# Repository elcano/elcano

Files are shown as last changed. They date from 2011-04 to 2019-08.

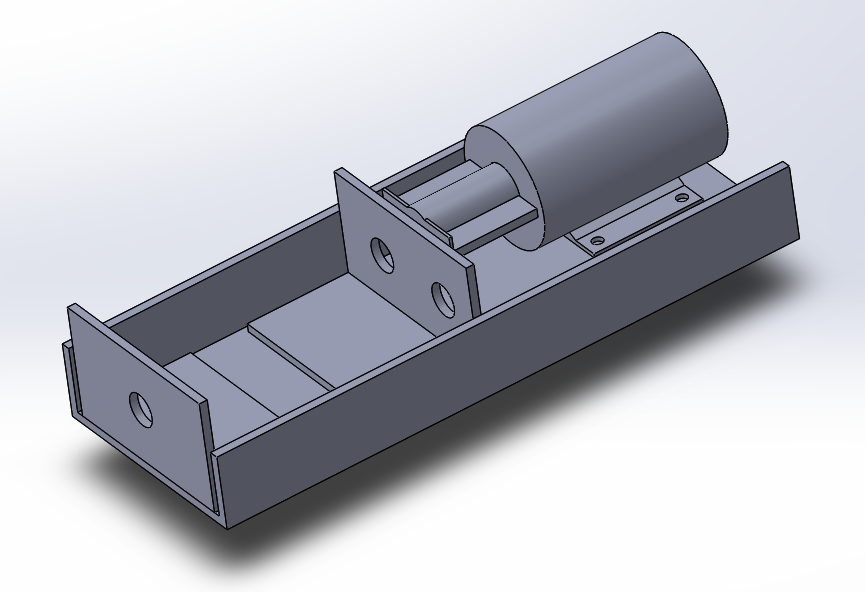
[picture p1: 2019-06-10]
Mechanical/ELF/Brake_System/Brake_System.PNG

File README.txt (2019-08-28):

Welcome to the Elcano autonomous tricycle project!
Please see:
http://www.elcanoproject.org/

This repository has been archived. The system consists of several different microprocessors. Elcano/Elcano has been broken into separate repositories for each processor.

To get started, fork and clone the repository:
https://github.com/elcano/elcano

Parameters and settings for each trike are defined in:
/libraries/Settings/Settings.h

Place the contents of the libraries folder into your libraries folder under
Arduino/libraries

The repository includes examples in the file:
Arduino/libraries/Settings/SettingsTemplate.h

Only libraries/Settings/SettingsTemplate.h should be committed in the
repository -- the Arduino/libraries/Settings/Settings.h file is site-specific.

-- Copy
   Arduino/libraries/Settings/SettingsTemplate.h
   to
   Arduino/libraries/Settings/Settings.h
-- Give your trike a different VEHICLE_NUMBER value.
-- Add your own trike's settings, following the examples.
-- Put your settings in a conditional for your new VEHICLE_NUMBER value.

When you pull in updates from the main repository, look for changes in
SettingsTemplate.h and if needed merge them with your own Settings.h.
Especially watch for new trike parameters used in sketches.

Sketches that need these settings should
#include <Settings.h>
*after* all other includes or definitions that are used in Settings.h.

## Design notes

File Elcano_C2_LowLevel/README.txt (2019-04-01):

In Settings.h
DEBUG enables serial printing of debug messages
RELAYInversion 
LLBversion defines which settings file should be used for the low level board

TESTING disables including hardware specific libraries like Arduino.h
testing is defined in the source code for unit testing

The libraries you will need are:
CAN_BUS_Shield by Seeed-Studio	
	https://github.com/Seeed-Studio/CAN_BUS_Shield

PID by Brett Beauregard
	https://github.com/br3ttb/Arduino-PID-Library

Pin Change Interrupt by Nico Hood
	https://github.com/NicoHood/PinChangeInterrupt

Builit-in 
SPI library
Servo library

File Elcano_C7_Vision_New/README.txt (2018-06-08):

Elcano Line Detection:

Updated 4/2/2018
Author: Conor Van Achte

How to use:
1. Make sure the Raspi Camera is detected by the OS by running this 
   command in console "vcgencmd get_camera".
2. If the camera is connected, you may need to enable the camera for use.
   This can be done by entering the command "sudo modprobe bcm2835-v4l2".
   This command opens up the camera for use by the OS.
3. Compile the program by running entering "g++ -std=c++11 $(pkg-config --libs --cflags opencv) -o LineTest LineDetectionMain.cpp" in console.
   (Optional) To run the program with communication to arduino add rs232.c to the compilation string.
4. Run the program with ./LineTest.
5. Exit the program by pressing the ESC key.

How does it work?

The Elcano Line Detection works by use of the Raspi Camera on the Raspi. As of 4/2/2018, the Line Detection code detects yellow lines, and 
has a filter for yellow colors. The program takes a frame as input from the camera, uses a yellow filter mask
on the image to isolate the yellow colors, and then applies a Gaussian blur to smooth out the image.
A Canny edge detector is then applied to the frame to detect the edges found in the image.
Finally a HoughLine transform is performed to draw detect lines on the image. The Elcano Line Detection program will then find the average
of the lines found, and draw an averaged line on the frame every 5 frames.This code is currently in testing
and will need refactoring and possible a new implementation for full lane detection.

Update 05/03/2018

Elcano Line Detection code has been refactored and appears to be working reasonably well with the arduino sketch Kyle Farmer wrote. The Line Detection
program is running much smoother after a reduction in GaussianBlur from a 25x25 matrix down to a 9x9 and finally to a 3x3. The Pi sends information to the
arduino mega, which then provides instructions to the servomotor on which direction to turn. Currently we have a Raspi connected to
an arduino mega via serial connection, and the arduino mega is connected to a small servo motor that rotates based on the values found by the raspi.

Additional Information:

The Elcano Line Detection code was written using Visual Studio. In order to compile you may need to install the additional libraries provided by
OpenCV. A link to setup Visual Studio with OpenCV can be found here: https://www.youtube.com/watch?v=l4372qtZ4dc.

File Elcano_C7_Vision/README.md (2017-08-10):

Elcano Vision Subsystem
=======================

This is the subcomponent of the Elcano project that uses a Raspberry Pi
to scan the area for obstacles with OpenCV.

Dependencies
------------

- [opencv (v3.2)](http://opencv.org) (object detection)
- [raspicam](https://github.com/cedricve/raspicam) (raspberry pi camera interface)

Build Instructions
------------------

1. Compile rs232:
	gcc -c rs232.c -o rs232.o

2. Compile main:
	g++ -std=c++11 $(pkg-config --libs --cflags opencv) -o main main.cpp rs232.o

Developer Overview
------------------

- `main.cpp`: The driver function
- `rs232.c`: Allows serial communication between Raspberry Pi and Arduino

Todo
----

- Improve reliability/accuracy of cone location with Kalman Filter
- Add makefile for building
- Add comments to main

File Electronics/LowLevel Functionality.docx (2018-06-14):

This document:

License:

Functionality:

The LowLevel is a printed circuit board (PCB) designed for land vehicle control. It acts as a daughter board (shield) for an Arduino Mega microcontroller. It is a dual-mode controller, which selects manual drive-by-wire control or autonomous computer control of the following:

- Control of the hub motor.
- Control of the turning servo.
- Control of the braking servo.

Input for drive-by-wire control comes in from either a joystick or an RC receiver. Autonomous control is provided by a stack of three additional microcontrollers (High Level Control):

- C3 (Pilot): Senses dynamic obstacles and sends near-term path and speed to C2.
- C4 (Path Planner): Computes optimum path from current position to destination, disregarding dynamic obstacles.
- C6 (Navigator): fuses instruments to give the best current estimate of position.

The connectors on the LowLevel are:

- X2 Cruise (DB25F) - Autonomous control signals from High Level.
- X3 Motor (DB15M): Signals for motor and drive-by-wire
- X1/X5 Turn Sensors (RJ45): SPI turn sensor digital inputs.
- X4 (ODO): Cyclometer (reed switch) input jack.
- JP9 (8 pin): Joystick analog input signals.
- JP12 (3 pin): PWM output signal to steer.
- JP11 (3 pin): PWM output signal to apply main brakes.
- JP5 (4 pin): Left steer turn sensor analog input.
- JP6 (4 pin): Right steer turn sensor analog input.

The LowLevel runs on 5V power, which it provides to sensors and servos on JP9, JP12, JP11, JP5 and JP6. A 9.6V battery supplies Vin to the Arduino, which regulates it to 5V and 3.3V. The RJ45 connectors send Vin, which must be regulated on the other end to 5V. Our trike uses a 36V battery to drive the hub motor and a 12V battery to drive the steering and brake servos. Each of these three actuators has a separate electronic subsystem, which generates 5V, but are not used by LowLevel. The 5V supply from the motor is used as an indication of whether 36V power is switched on.

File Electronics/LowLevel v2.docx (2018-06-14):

LowLevel v2.1 PCB

This document contains:

- Schematic:
- Board layout:
- Assembly guide:
- License:

Wiring Schematic:

- Refer to connections spreadsheet for pin mapping (still in progress)

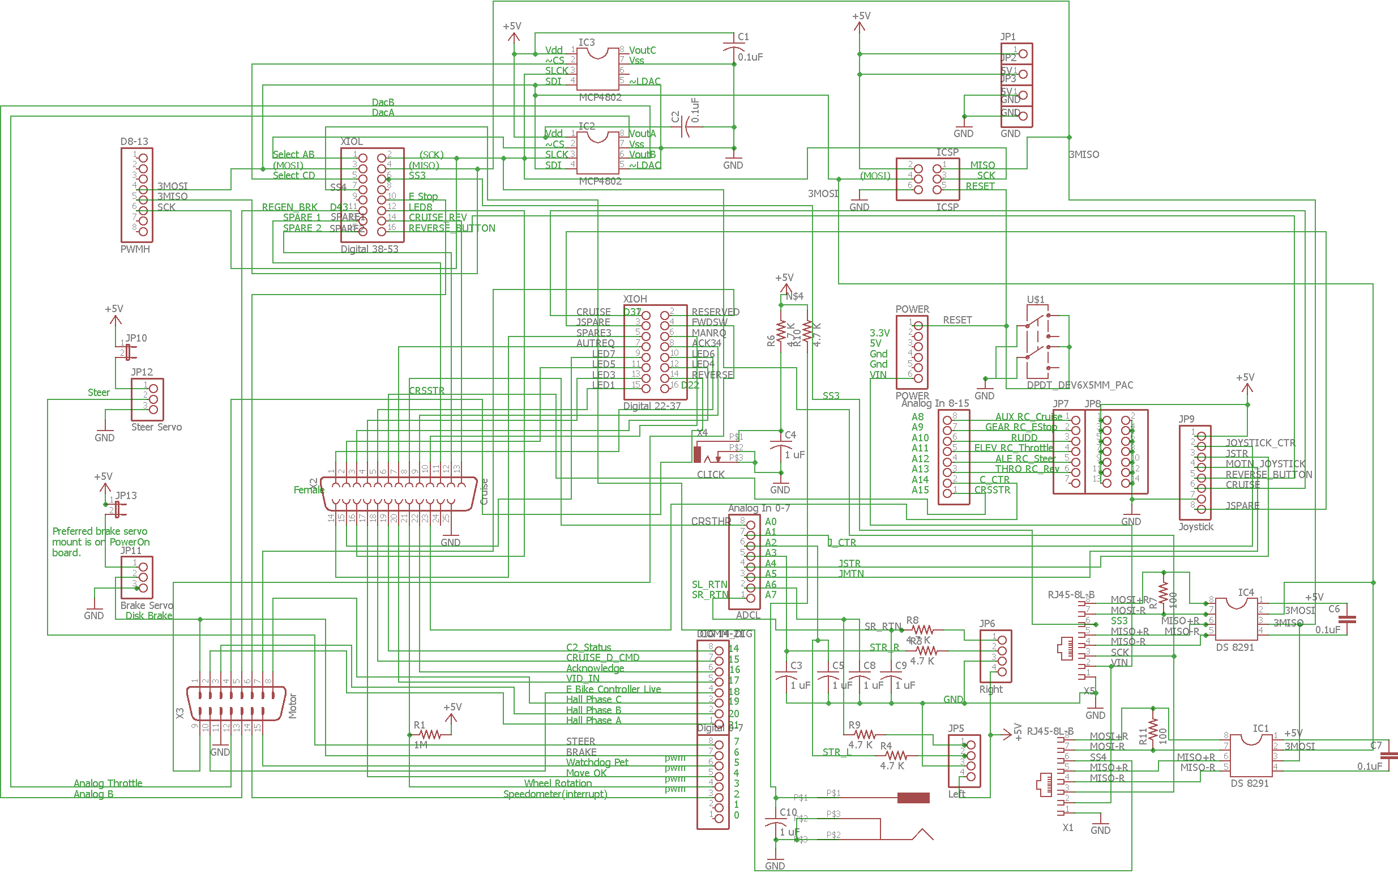
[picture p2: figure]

Board Layout:

- Shown without routing for layout purposes

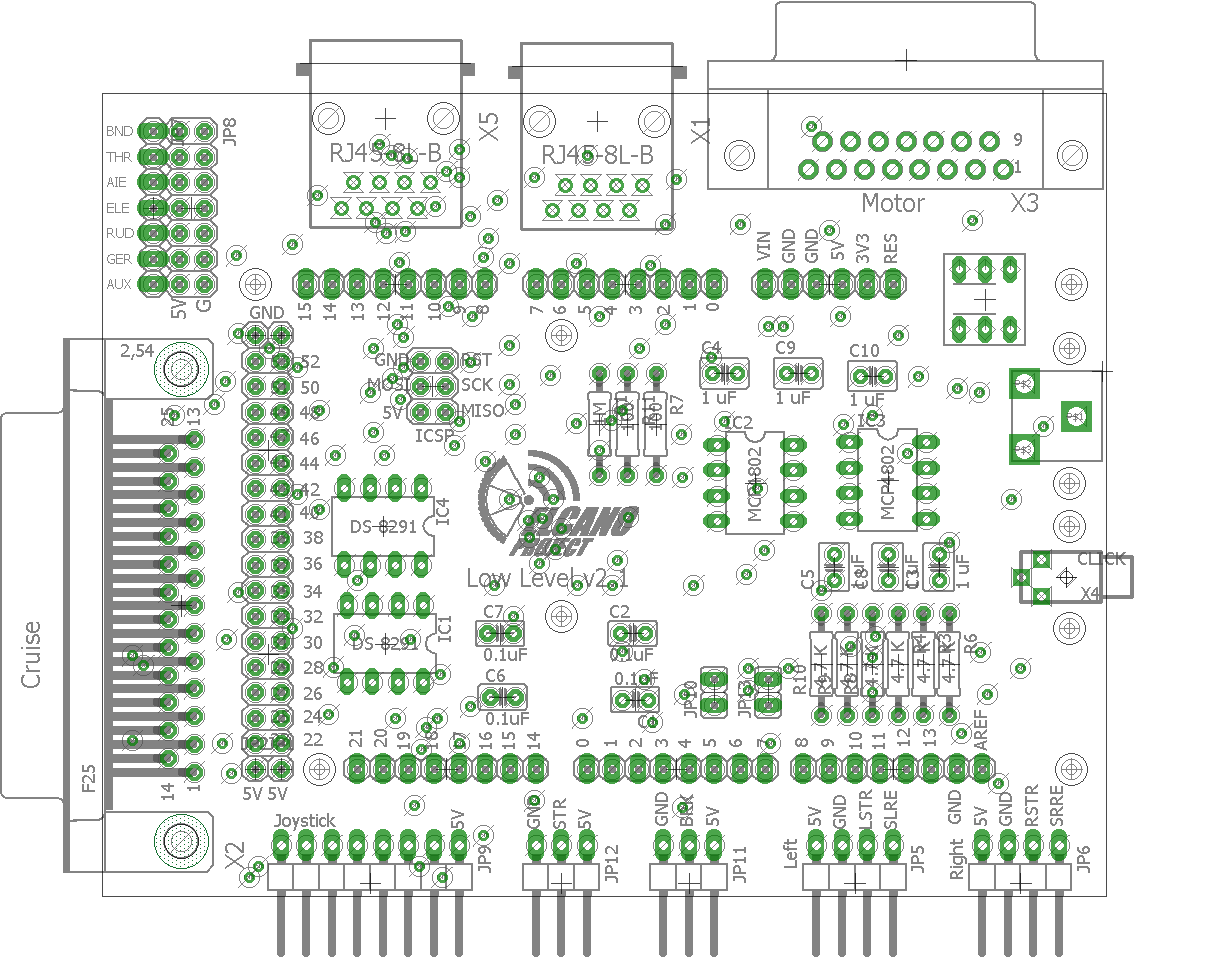
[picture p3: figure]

Assembly Guide:

- Begin with soldering on the header connectors for the Arduino, hold them in place with masking tape and make sure they are straight before soldering them on. This ensures proper mating with the microcontroller which is crucial. The female end of the header is on the top of the board and the male ends are on the bottom.

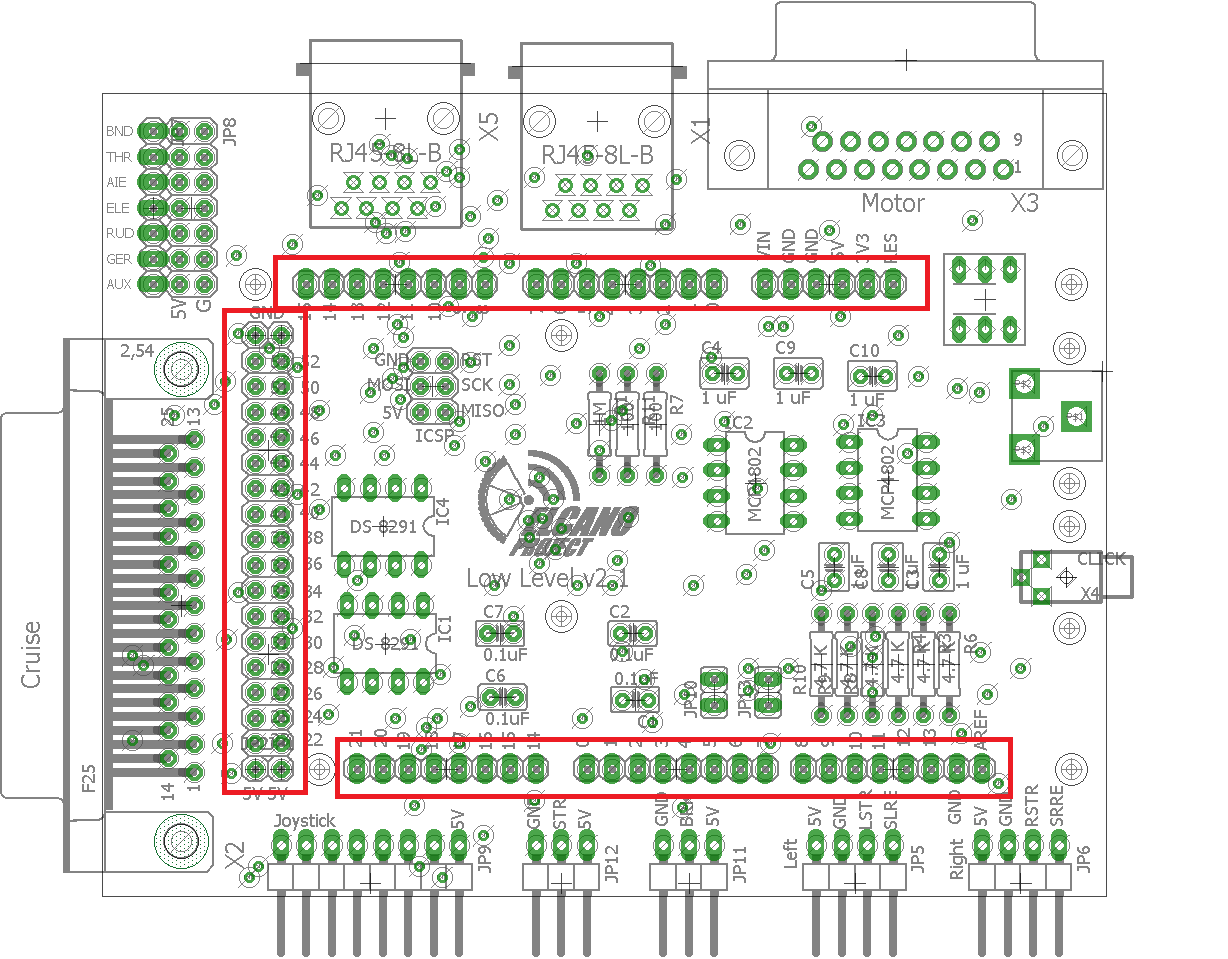
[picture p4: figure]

- Next install the peripheral connectors, all of these are mounted on the top of the board. The D-15 connector is male and the D-25 connector is female. Be precise when soldering in the 3 sockets for the RC.
- The connectors on the bottom row can be on the top or bottom side; straight or right angle. The choice depends on the connectors and board mount.

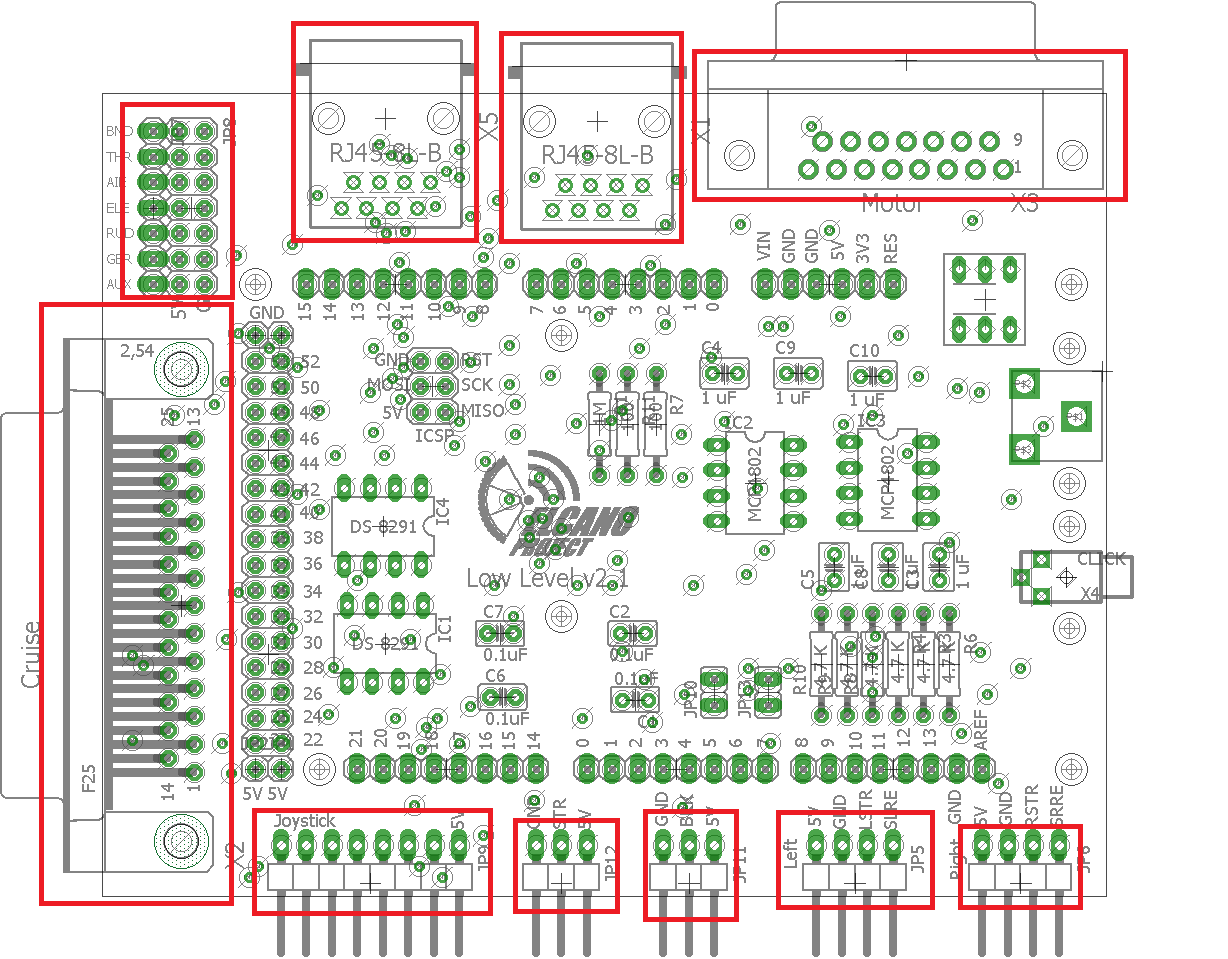
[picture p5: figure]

- Next install components:
  - Integrated Circuits
    - Option to solder in sockets first to allow for quick swapping of IC’s.
  - ICSP
    - Pins extending on the top of the board.
  - Reset Switch
    - Align small rectangle on switch with parallel lines on the layout for direction.
    - It may be desirable to leave off the relay switch, since it may occupy space needed for an Arduino shield.
  - Power Jack
    - The holes on the board are big so make sure ample solder is used.

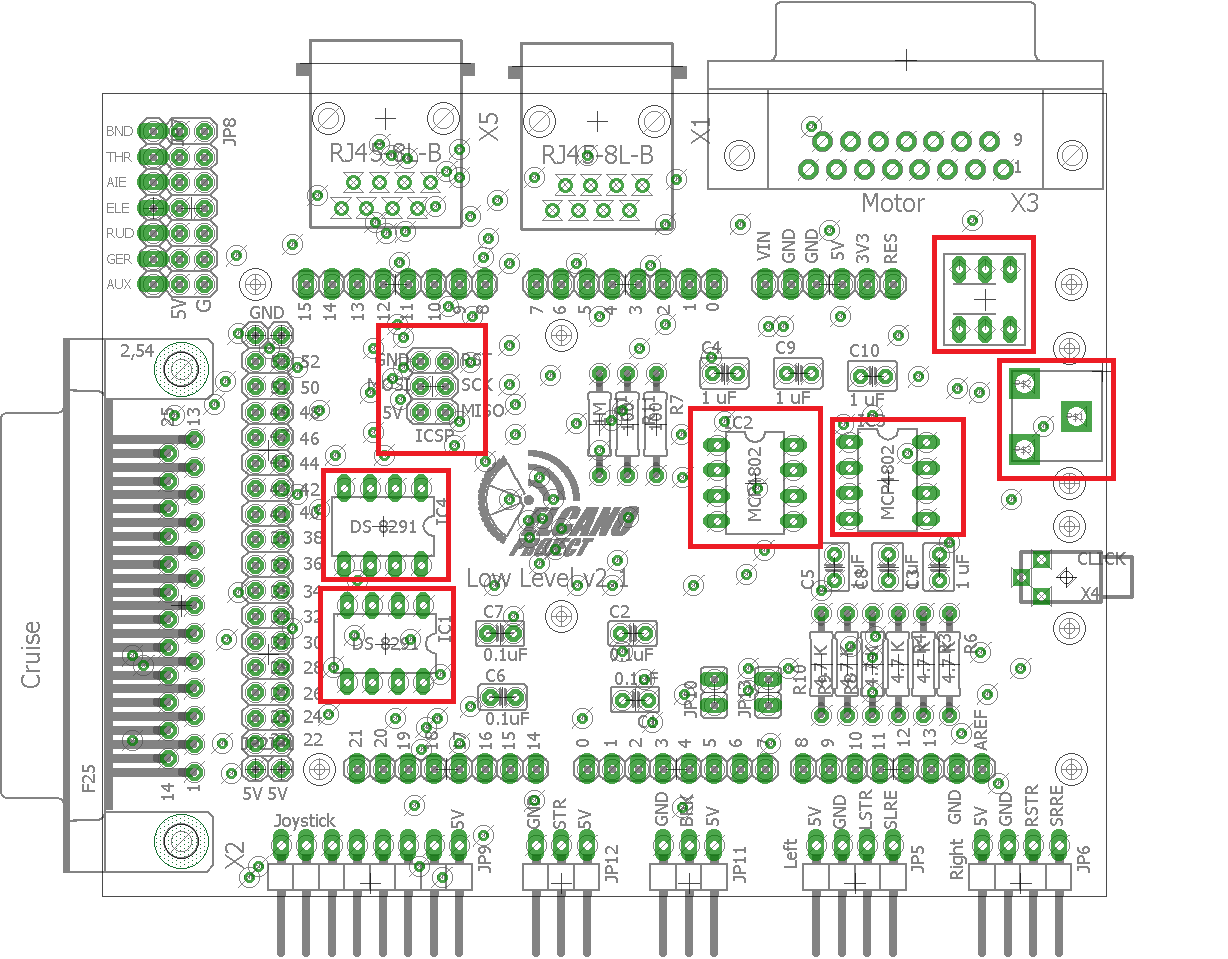
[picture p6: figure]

- Finally install resistors capacitors and jumpers
  - Make sure that all parts sit below the level of the Arduino headers so they don’t get in the way.

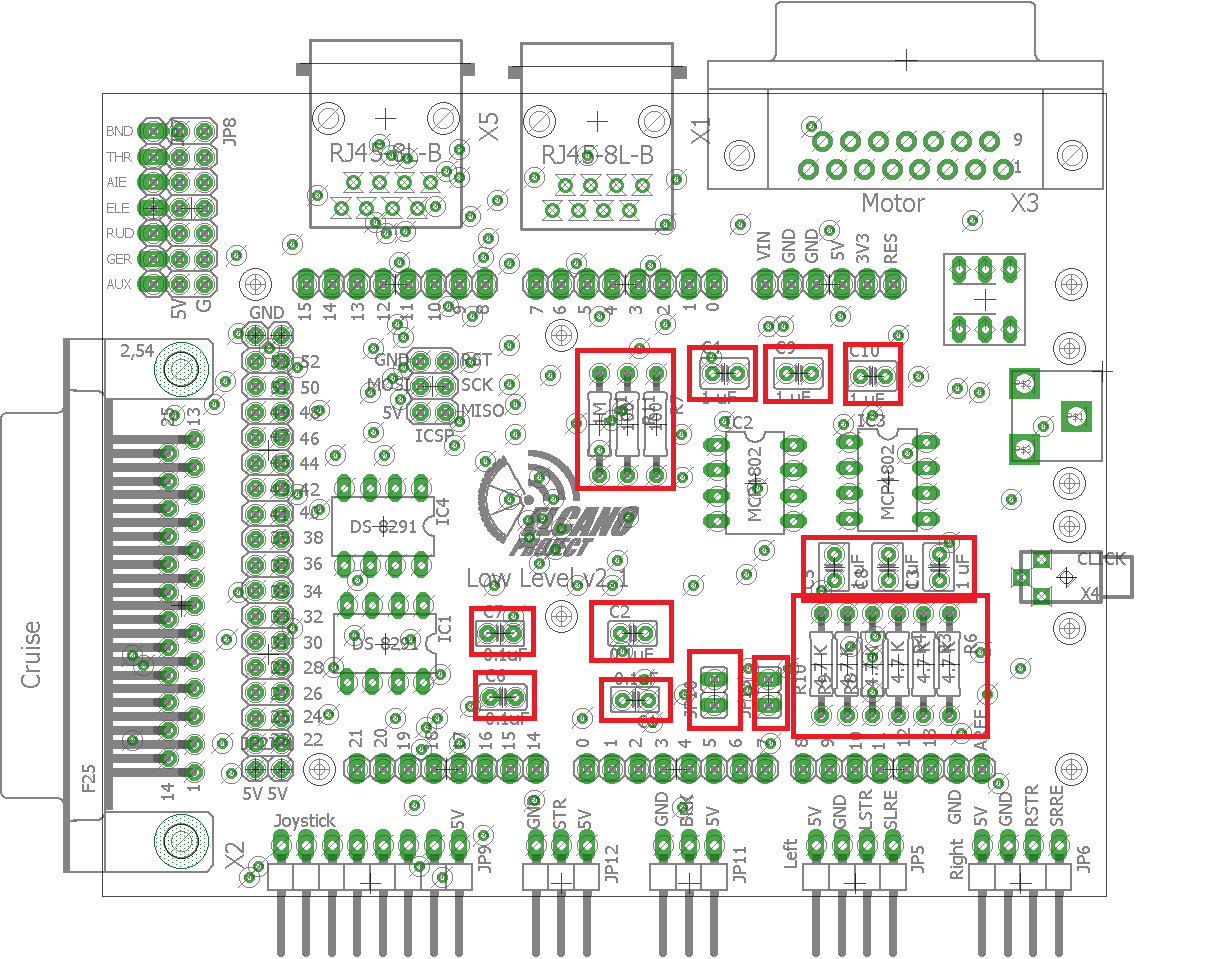
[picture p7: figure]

- When you’re finished the board should look like this.

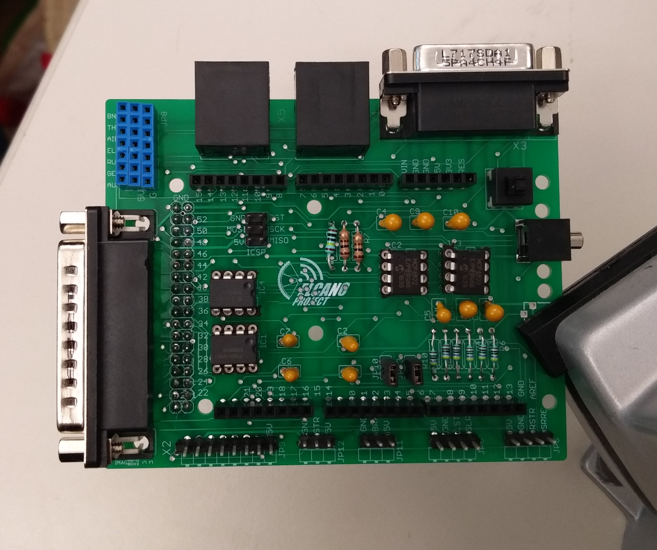
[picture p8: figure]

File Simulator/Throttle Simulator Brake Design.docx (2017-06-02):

Paul Curry, Elcano Project

Names of people working on visualization for the simulator:

Joe Donan: jedonan@gmail.com

Coover Mackne: kubermotgi@gmail.com

Design for Throttle Simulator with Brake

The brake will be factored into the velocity equation with a

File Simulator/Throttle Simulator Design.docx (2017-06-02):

Paul Curry, Elcano Project,

Design for Throttle Simulator: A simple start for a trike simulator

The throttle simulator is a .ino that will run on an Arduino mega. The low-level board, which is a mega attached to a wrapper board, will plug into the simulator to send and receive information. The simulator will act as a simulated trike version 1.

The trike sim will sit in a loop sending speed pulses to the low-level board based on its current throttle value (initialized at 0). The trike sim will receive an analog throttle voltage from the Low-Level DAC. This voltage will be read with analogRead(PIN = 0) which maps input voltages between 0 and 5 volts into integer values between 0 and 1023. As stated above we will read the analog input through analog pin 0 on the simulator.

The trike sim will continuously send digital pulses to the Low-Level board to simulate the pulses from the wheel cyclometer on the trike at a speed based on the throttle value it has last read from the low-level board. The pulses will be sent out of digital pin 1 (serial out on the mega) so that a monitor connected via usb can also read the pulses being sent out. The pulses will be sent to digital pin 3 on the Low-Level Board’s mega (IRPT_WHEEL is defined as 3 in the SettingsTemplate.h, if this changes then the trike sim will break!). These pulses trigger interrupts which call the WheelRev function in Elcano_C2_LowLevel.ino.

Todo: get the mapping,

check if will run w/o angle

Note: A = analog

Low-Level: Trike Sim:

Throttle -> Analog <- Speed (Pulse)

(A0 to A0) (D2 to D3)

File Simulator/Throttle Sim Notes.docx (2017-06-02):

Paul Curry, Elcano Simulator Notes

Upwards throttle

Data 2

- 227 max throttle
- 3 second ramp to max throttle
- 13.5 m/s max speed
- 4 second to max speed
- 1.3 sec to first reaction

Data 3

- 227 max throttle
- 0 second ramp to max throttle
- 13.5 m/s max speed
- 1.6 second to max speed
- 0.6 sec to first reaction

Data 4

- 94 max throttle
- 5 second to max throttle
- 1.613 max speed
- 6.7 sec to max speed
- 2.7 sec to first reaction

Data 5

- 227 max throttle
- 5 second ramp to max throttle
- 6.6 m/s max speed
- 5.9 full speed
- 2.3 sec to first reaction

Physical parameters: ((z(tick)/s))/(1570.7963(mm)/s)=x(mm)/s→z=x*WHEEL_CIRCUM(mm)/s

1st Model linear function: f(throttle, time)

Cut off speed at 0

Average reaction time: → f(t,1.725) = 0

f(throttle, time) = throttle * CONST * (REACTION_TIME – time)

2nd Model from previous data: f(throttle)

Cut off speed at 0

O(t)=

max⁡( M_t ,N_t )

M_t =O_(t-1) *0.9296008 (must be mass of trike or something)

N_t = max(0,(L_t -65)/((227-65)*13600))

L_t = (∑_(z=(t-7))^t C_z)/8

→O(t)=WHEEL_CIRCUM*max( 0_(t-1) *0.9296008,max(0,((∑_(z=(t-7))^t (C_z)/8-65))/((227-65)*13600)) )

Implementation notes: Create buffer of 10 throttle values so get throttle means

Actual Physics

C_v =velocity

n=mechanical efficient ~.98

m=mass of vehicle

g=acceleration due to gravity

C_r =co-efficient of rolling resistance

a=acceleration

s=slope

m_w =mass of wheels

p=air density sea level

C_w =wind speed

W_r =(C_v)/n*m*g[C_r +s/100+a/(g(1+(m_w)/m))]

W_D =(C_v)/(2n)C_D *A*p(C_v +C_w )^2

Simplified (no head wind, change of area, gravity ect)

W_D =R_1 C_v^3

W_r =R_2 *m*C_v [R_3 +s/100+aR_4 ]

R_1 dependent on C_v ,

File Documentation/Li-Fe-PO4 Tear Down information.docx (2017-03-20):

Li-Fe-PO4 Tear Down-Documentation:

Description:

On March 15th, 2017, a teardown of one of the Li-Fe battery cell blocks was conducted for both educational and troubleshooting purposes. This document is created such that anyone whom the internal structuring of such batteries interests as well as a reference point as to what a functioning charging controller may look like.

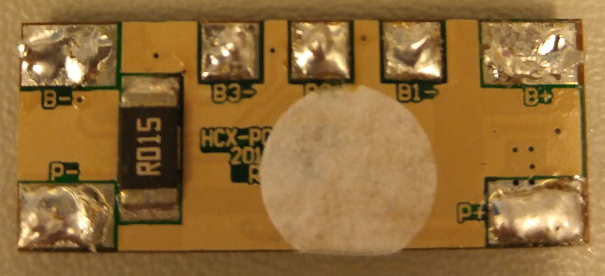
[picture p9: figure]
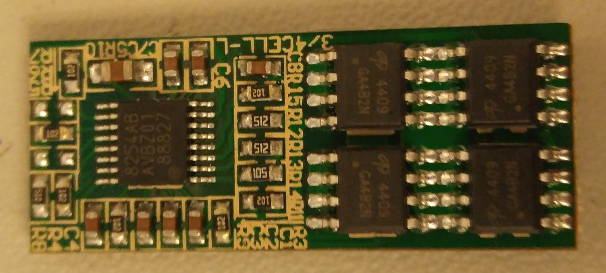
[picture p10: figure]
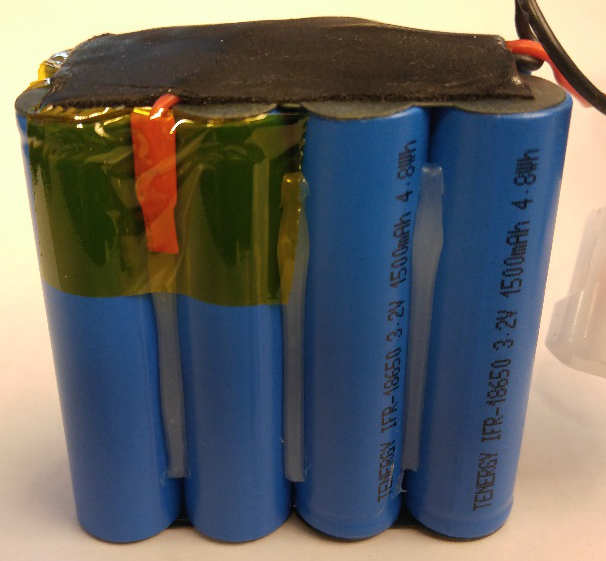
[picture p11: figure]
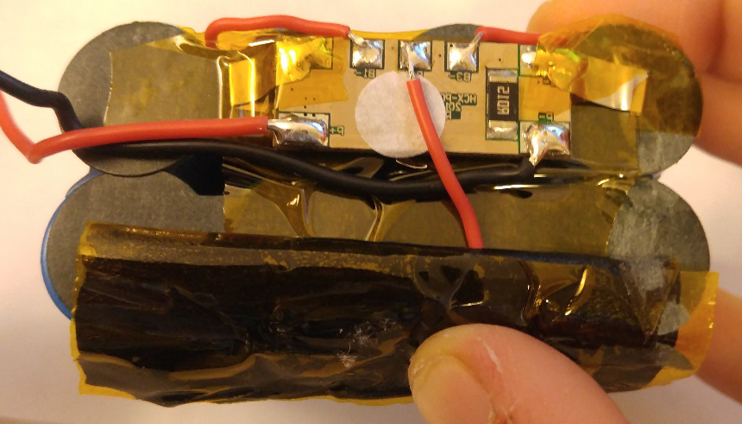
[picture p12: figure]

As seen in the illustrations above, the Cell block consists of eight individual cells, each with a rating of 3.2 Volts meaning that they are connected parallel in pairs which are then in series with each other. Further analysis into which cell is faulty was not conducted as there was no physical evidence that the charging controller was faulty. Based on this assessment and further performance test it was decided that one of the cells cuts out after a certain period of time under load or at a certain operation temperature.

For any further information about the batteries refer to manufacturer dependent Datasheet.
Single cell type: LiFePo4 18650 3.2V 1500mAh 4.8Wh

Tear Down conducted by Tim Kostersitz, EE – reachable at: timkos@live.at

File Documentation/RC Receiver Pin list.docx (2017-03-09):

RC Receiver Pin list and interconnections between RC Shield and C2

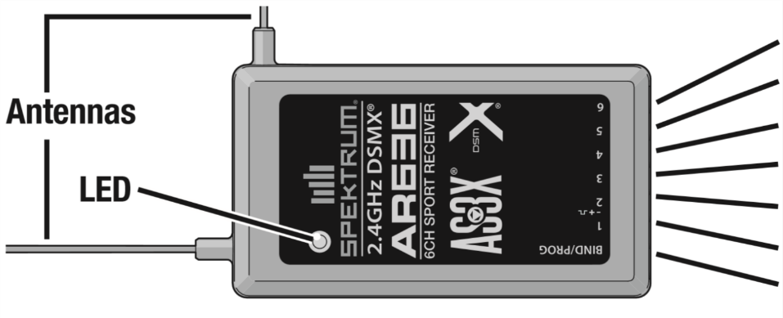
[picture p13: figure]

7.
6.
5.
4.
3.
2.
1.

Receiver Pin # | Arduino Pin # | RC Controller Function | Programmed Trike Func.
1 | | ---
2 | 18 | Left Stick Up/Down | Brake
3 | 21 | Right Stick Left/Right | steering
4 | 19 | Right Stick Up/Down | RC Go
5 | | ---
6 | 20 | E-Stop | E-Stop
7 | (17) maybe | Flap/Gyro | ---

RC Shield Shematic and visual explaination:

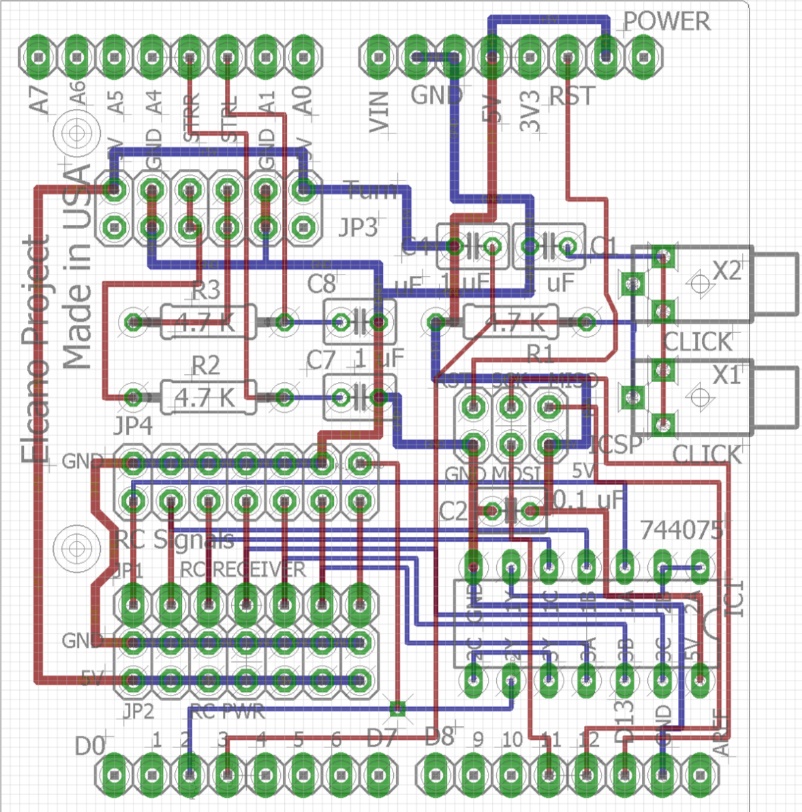
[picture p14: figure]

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
Jumper plug-ins (to Arduino)

RC Receiver plug-in

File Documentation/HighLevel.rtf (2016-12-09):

High Level Board

The High Level Circuit board replaces the MegaShieldTrio. The Trio connected three Arduinos:
• C6 Localization (Navigator)
• C4 Mapper
• C3 Pilot

On the original Trio board, C6 was an Arduino Mega and C4 and C3 were Arduino Nanos. On the new board, C3 is an Arduino Micro. The C4 program has grown too large for the smaller processor, and it is now an Arduino Mega. The High Level board will be populated by
• Arduino Mega C6 Localization processor
• Adafruit Ultimate GPS Shield
• AdaFruit LSM303 Compass/Accelerometer
• Arduino Micro C3 Pilot
In addition, the C6 Localization processor communicates with C7 Vision, hosted on a Raspberry Pi. The C3 Pilot controls one or two C5 Obstacle Detection units. Processors C7, C6, C5, C4 and C3 form the high level system. The high level system connects to C2 and C1 which form the Low Level system, designed to make the vehicle implement the commanded speed and turn.
The LMS303 compass is plugged into either X5 or X8, depending on desired orientation. Only one compass should be used.
JP5 is a nine-pin connector to the C4 Arduino Mega Mapper. One pin from JP5 is connected to the Reset pin. The other 8 pins are a straight connection to pins D14-D21 on the Mapper.
Interchangeable connectors X1 and X4 go the the C5 sonar obstacle detection unit. The cables are physically RJ-45 Ethernet cables, but the signals are not compatible with Ethernet.
Power and ground to all microprocessors is supplied from VIN (about 9.6V) which is connected directly to Arduino Megas and to the Raspberry Pi, which regulate the power to 5V. The Megas pass VIN on to C3 and C5, which have their own voltage regulators.
X7 is an interface to an Optical Mouse (Optical Flow) sensor. This instrument uses optical odometry to find two-dimensional changes in position.
Connector X2 is a DB25-pin cable connecting to the Low Level board. The C3 Pilot outputs desired speed and turn as serial commands to the C2 Low Level processor. C2 returns actual steering and brake angles to C6 over serial. Serial communication is a ring from C6 → C4 → C3 → C2 → C6. There is secondary serial communication between C6 and C7 over USB. Communication between C3 and C5 uses SPI.
The mouse and compass are normally connected to 5V by placing a jumper in JP1 and JP3. Those parts regulate the voltage to their internal 3.3V which is available on JP2 and JP4. These jumpers are usually open, since connecting would produce conflict between sensor produced voltages and Arduino produced voltages.
Jack X3 permits direct input of cyclometer data (reed switch once per wheel revolution) that can be used to compute speed. In normal operation, C2 performs speed calculations and passes the command over serial.
The high level board contains a two-channel digital to analog converter (DAC) that would allow C3 to send analog voltages to C2. The preferred method is to send information as serial.

Other documents
• HighLevel.xlsx – Signal connections between the processors.
• HighLevel.sch – Eagle CAD schematic
• HighLevel.brd – Eagle CAD board layout.
• HighLevelBOM.xlsx – Bill of Materials.
• http://www.plcdev.com/plc_musings/tim_young/eagle_cad_to_gerber – Gerber files.
• https://www.pcb4u.com – Prototype board fabrication.

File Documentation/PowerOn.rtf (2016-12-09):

Power-On Circuit Board

The power-on circuit board's functions are:
• Supply precharge resistor (R2) and diode (D1) for Kelly KEB or KBX e-bike controller.
• Handle Emergency-stop.
• Provide clean wiring between E-bike controller, hub motor and low-level Arduino.
• Provide a 5V digital speed signal from the hub motor.

Kelly Power
Kelly e-bike controllers specify a power-on circuit. When the power switch (SW1) is off, there is no voltage on X3-6 to the e-bike controller, and it is thus off. When the switch is turned on, the e-bike controller receives the 36V that it needs to operate. This is a low-power signal, and is limited by the 2A fuse (F1).
The main 36V supply from the battery (X5-3) always goes to the hub motor (X5-3). When the controller is on, this line can draw as much as 25A. When SW1 is off, relay K2 is also off, and the main 36V line needs to pass though the 10K resistor R5.

Emergency-stop
There are two sources of e-stop.
1) An e-stop can be commanded by the C2 low-level Arduino via X1-6. This line goes into pin D7 of the Arduino Micro (C1) on the Power-on board.
2) The C2 low-level computer is required to periodically send a signal to X1-15, which is received on D13. If this signal is not received, the C1 Arduino assumes that C2 has ceased to function and C1 applies an e-stop.
Arduino C1 is powered by 5V signal produced by the brake actuator (JP5-2) from its 12V supply. It is thus on a separate supply from all other Arduinos and has power as long as the brakes have power.

On set-up, the C1 Arduino applies a PWM signal on D5 that would apply the brakes. This signal does not get used until e-stop is activated. When the C1 Arduino applies e-stop, it outputs a signal on D8, which is amplified by buffer IC1B so that it has the power to drive relay K1. This relay contains switches S1 and S2. When the relay is activated, S2 removes 36V power to the e-bike controller, turning it off and disabling the hub motor. In normal operation, the brake state commanded by C2 on X1-1 is sent to the brake actuator. In an e-stop, S1 replaces the normal brake signal with a brake stop signal.

Wiring
A standard DB15 cable connects the PowerOn board (X1) to the LowLevel board.
The brake actuator is attached to a standard 3-pin servo pin (JP5).
Power and ground from the 36V battery comes in on X5, which sends main power and ground out to the e-bike controller.
Power (5V), ground and Hall sensor signals come in from the hub motor on either X2 or X4. These signals are then relayed to the e-bike controller on X4 or X2. On the Kelly KBX, these are the signals from the 6-pin connector.
Other signals from the Kelly 9-pin connectors come in on the DB9 connector (X3).

Speed Signal
A Hall signal from the hub motor can be used to measure speed. The signal from the hub has ben observed to have a greater than 5V range, and is not a square wave. The low-pass filter (C4 and R4) is meant to remove noise. The signal is then passed though IC1A, which forms it into a 5V square wave. The speed signal is then passed to the low-level computer via X1-14.
Another option is to use the Arduino Micro to process the three Hall sensor signals. These feed into pins D0, D2, and D3 on the Arduino, which support interrupts. The output speed from these three signals is on D6, which supports PWM.
Jumper JP5 is used to select which speed signal goes to the low-level processor. It can either be the signal that is only filtered by hardware, or it can be the signal from the C1 Arduino.

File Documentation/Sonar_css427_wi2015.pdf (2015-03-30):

## Scott Stewart, Tim Galvin T. Folsom CSS 427 13 March 2015

# Range Sensor

# Problem Addressed

## The problem addressed by our team was to develop and test the functionality of a sonar board for use in the Elcano project. The sonar board uses multiple sonar sensors simultaneously to gather range data of its surrounding environment. Each sonar board uses

eight sonar sensors: one at each hour of the top half of the clock, and one behind.

## Harmonious operation of sonar sensors, their scope, and communication were problems to

address.

# Work to be Done

Existing datasheets and empirical data were to be used to determine a correct manner to poll sensors in a way that is efficient. The datasheets were also to be used to analyze any overlap of the sonar sensors. Code needed to be written to handle the coordination of the timing of the sonar sensors and the communication between them and the microcontroller using SPI. The code was to be robust and usable by others that work on the Elcano project.

# Solution

## Software Design

Our solution uses an Arduino microcontroller to communicate with the sonar board using SPI bus to coordinate the sonar sensors. The sonar sensors were put into groups of two or three sensors per group. A round of sensor data is gathered by simultaneously getting and reading range data from all sonar sensors in a group. The groups are pinged for data once per round in a set order. As a result, data is received in an orderly manner without much interference between sensors.

## The defined rounds of polling using position on an imaginary clock as position

| Sensor 1 | Sensor 2 | Sensor 3
Round 1 | 12 o’clock | 3 o’clock | 9 o’clock
Round 2 | 1 o’clock | 6 o’clock | 10 o’clock
Round 3 | 2 o’clock | 11 o’clock

## Rounds are handled by driving pins corresponding to a given group HIGH or LOW depending

on which group’s turn it is to get sonar data. This is handled in our setRound() function that takes two integers representing high and low order bits for each group.

The sensors themselves send a PWM signal that is read via an interrupt that records the time length of the signal. This time is then processed and converted into a range measurement in centimeters. This data is then printed.

## Test Methods

We were faced with the problem of testing whether our code worked or not without having the new sonar board on hand. As a solution, we set about building a wooden jig that would hold the sensors in their correct orientation, and allow us to get meaningful readings from them.

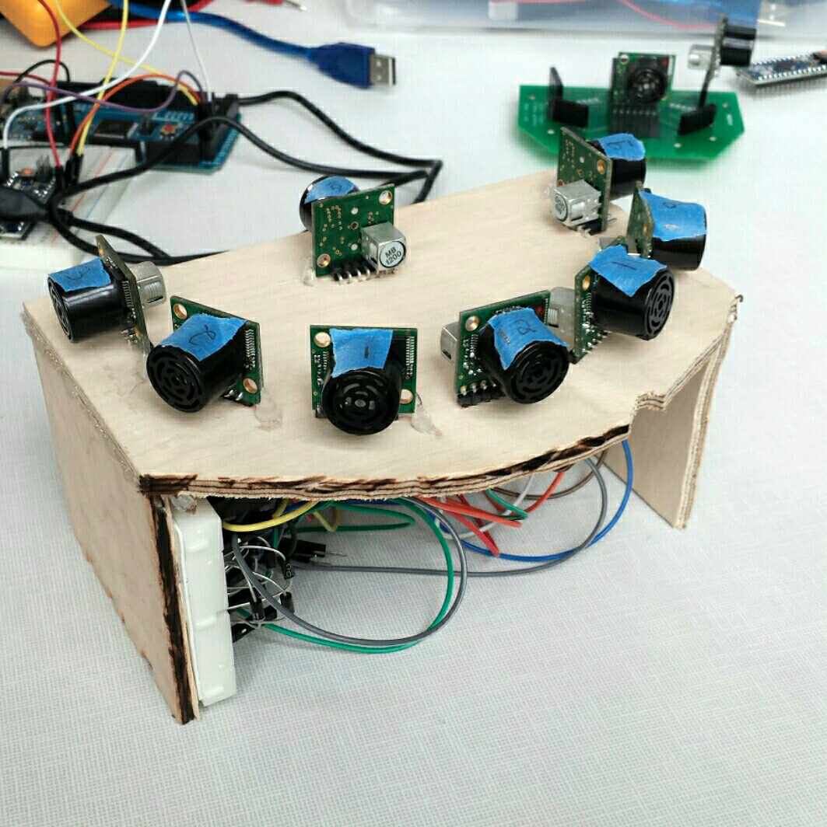
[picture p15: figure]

## Our makeshift “sonarboard”

Once we had the sensors in place, we were able to take the sonar board outside and test our ability to get raw data. In the beginning, this simply meant looking at a series of numbers in the serial monitor. This was useful data, but it was still difficult to convince ourselves that the data was legitimate without some sort of visual.

## Enter processing.org. This opensource project allows for the rapid development of

visualizations, and works very well with serial data. Using built in libraries, we were able adapt

## an example program written by Christan Marc Schmidt [1] (which shows random radii pie

slices) to read serial data and give us a visual of the data from the sonars.

## The program works by reading in a series of values from the given serial port, and then

mapping those values to the radius of a given “slice” of the pie.

Output showing obstacles at 11 and 1 o’clock.

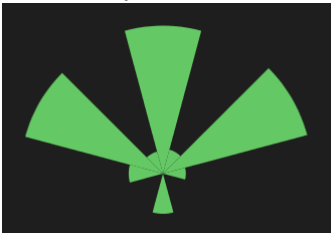
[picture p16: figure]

## We discovered that noise was rampant anytime we tested indoors, but the readings seemed

very reasonable once the board was outdoors.

## Physical/Mechanical Considerations We were aware throughout our testing that our wooden board was likely not ideal for using the sonar sensors. The sensors are angled correctly in terms of yaw, but they are able to

wiggle their pitch somewhat.

Also, our knowledge of circuitry isn’t as robust as our coding experience, and we admit there

## may be some additional circuitry needed for reliable measurements. For example, we spent

many hours wondering why we couldn’t get readings from multiple groups of sensors, only to

## find out that we needed diodes in series with the PWM output from the sensors in order to isolate them from each other. This of course will be a moot point once the new fabricated

sonar boards arrive.

## SPI Communication

We weren’t able to achieve reliable SPI communication in the time that we had. Currently the code will successfully send data over Serial from the sonar arduino.

The interaction of sending a command from the master, having the master wait for a reply, and then reliably sending the 26 bytes needed proved to be very difficult. Simple single byte communication was trivial, and we were able to get data sent from master to slave and back

## again without any issue. However, when we moved to more complicated scenarios, things became more difficult. Here is a series of steps explaining what we were hoping to accomplish:

1. The master sends a command over SPI to the slave, indicating it wants sonar values.

## 2. The slave (sonar arduino) then goes into a mode of reading values from all sonar

sensors. During this time, the master knows to stay idle.

## 3. Finally, the slave has data to send back to the master and begins transmission back

over SPI.
4. The master is intelligent enough to know that the real data has begun being sent back, and stores the data accordingly.

## 5. The communication ends, the slave goes back into idle, and the master does what it

needs to with the data.

## References

## 1. Example Piechart with random radii. http://www.openprocessing.org/sketch/49035

## Source Code

We will post the code here for reporting’s sake, but we will also send the .ino files via Canvas message.

/*sonarboard*/
#defineIRQ2_PIN1 //pulse10,11or12 #defineIRQ2_ID3 //TheinterruptIDrelatingtopin1

#defineIRQ3_PIN0 //Pulseon6or9 #defineIRQ3_ID2 //TheinterruptIDrelatingtopin0

#defineSDA_PIN2// I2CSDA

#defineIRQ1_SCL_PIN3 //Pulseon1,2,or3;orI2C

#defineIRQ1_ID0 | //TheinterruptIDrelatingtopin3

#defineSNR_10_PIN4 //Analogin6isSonar10 #definePWR_SEL_PIN 5 //Use5Vor3.3V #defineSNR_11_PIN6 //Analogin7

#defineRND0_PIN | 11//Loworderbitforselectingtheround

#defineRND1_PIN | 7 //Hibitofroundselect

#definePWR_ON_PIN | 8 //Applypowertosonars

#defineFRONT_PIN | 9 //Donotdisturbifhigh

#defineREAR_PIN | 10 //Donotdisturbifhigh

#defineSNR_SEL_PIN SS //Chipselectfromhostprocessor #defineSNR_SI_PIN MOSI//Thisprocessor'sserialinput

#defineSNR_SO_PIN | MISO//Thisprocessor'sserialoutput

//#defineSNR_12_PIN | A0

//Inthisversionofthecode,weuseA1-A3to //Signalwhichsensorsshouldbetriggeredineach //round.Oncetherealboardarrives,thesecanbe //reclaimedastheroundswillbecontrolledby //ciruitryconnectedtotheRND0_PINandRND1_PINpins
#defineGROUP1_PIN | A1

#defineGROUP2_PIN | A2

#defineGROUP3_PIN | A3

//#defineGROUP2_SEL | A4
//#defineGROUP3_SEL | A5
//#defineSNR_3_PIN | A3
//#defineSNR_6_PIN | A4
//#defineSNR_9_PIN | A5

#defineTIMEOUT_PERIOD100//ms #defineROUND_DELAY100//msbetweenrounds,seemstohelpstability

//Whentrue,senddataoverSerial,falsesenddataoverSPI #defineDEBUGtrue

//WhensedningoverSerial,truegivesverboseoutput #defineVERBOSE_DEBUGfalse

/*Twoboardscanhold12sonarsonthepointsofaclock. ThefrontboardholdsSonar12(straightahead) and1,2,and3Ftotheright.
Italsoholds9F,10,and11totheleft. Therearfacingboardholds3Rthrough9R,with6Rpointingback.

ThefrontsonarboardusestheSPIinterfacetoappearasaslavetoahost computer.
Whenthehostasksforsonarreadings,thefrontboardsendsalldata.

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

Theremaybenorearboardpresent. Inthiscase,thefrontboardmayusethe9F socket.

Sonarsaregroupedintothreeroundssothatmultiplesonarscanfiresimultaneously and
notinteferewitheachother.Roundsareselectedbythe(RND0,RND1)signal, whichisusedasaGraycode(onlyonebitchangesatatime).

Round | Sonars

### 00 none

01 12,3,9
11 1,6,10
10 2,11
Aroundmayfireupto3sonars.Thesonarrangemaybereportedaseitherananalog value
orasapulsewidth.Apulsewidthwillcauseaninterrupt. Therearethreeinterrupthandlers,oneforeachsonarfiredintheround.
*/
//ModifyEXPECTED_SIGNALStomtchwhichsonarsareontheboard. #defineEXPECTED_SIGNALS13
#defineEXPECTED_SIGNALS23

#defineEXPECTED_SIGNALS32

#defineSTATE_INITIAL0

#defineSTATE_READY 1

#defineSTATE_ROUND1 2

#defineSTATE_ROUND2 3

#defineSTATE_ROUND3 4

#defineCOMMAND_GO1

#defineRANGE_DATA_SIZE13

#include"pins_arduino.h"

byteBoardCount=1; //justthefrontboard byteState=STATE_INITIAL;//initializing volatilebyteSignalsReceived; volatileunsignedlongtimeLeft; volatileunsignedlongtimeRight; volatileunsignedlongtimeBehind; volatileunsignedlongtimeStart; volatilebooleantimeStartSet; volatilebytevalueIn;
volatilebooleanprocessIt;

intrange[RANGE_DATA_SIZE]={0,0,0,0,0,0,0,0,0,0,0,0,0}; introundCount=0,timeoutStart=0,timeSinceLastRound=0; volatileintisr1Count,isr2Count,isr3Count;

voidsetup()
{
//SPISetup
pinMode(MISO,OUTPUT);
SPCR|=_BV(SPE);//turnonSPIinslavemode SPCR|=_BV(SPIE);//turnoninterruptsforSPI processIt=false;//falseuntilwehavearequesttoprocess

timeLeft=timeRight=timeBehind=timeStart=0; isr1Count=isr2Count=isr3Count=0; timeStartSet=false;
Serial.begin(115200);
pinMode(A1,OUTPUT);
pinMode(A2,OUTPUT);
pinMode(A3,OUTPUT);
pinMode(0,INPUT);
pinMode(1,INPUT);
pinMode(3,INPUT);
State=STATE_INITIAL;
BoardCount=1;
// | digitalWrite(RND0_PIN,LOW);
// | digitalWrite(RND1_PIN,LOW);
setRound(0,0);
digitalWrite(FRONT_PIN,HIGH); //signalrearboardthatwearehere;Seeifthere isarearboard
//select5Vpower
digitalWrite(PWR_SEL_PIN,HIGH);
//turnonsonars
digitalWrite(PWR_ON_PIN,HIGH);
// | for(inti=0;i<1000;i++)
// | { //Seeifthereisasecondboard
// | byteRear=digitalRead(REAR_PIN);
// | if(Rear==HIGH)
// | {
// | BoardCount=2;
// | //needtodynamicallyattach/detacyIRQ1_SCL_PINsothatitisshared
betweenIntRightandI2C
// | break;
// | }
// | }
| delay(200);//Personardatasheet,needs175msforboot
| attachInterrupt(IRQ2_ID,IsrLeft,CHANGE);
| attachInterrupt(IRQ3_ID,IsrBehind,CHANGE);
| if(BoardCount==1)
| {//don'tneedD3forI2C
| attachInterrupt(IRQ1_ID,IsrRight,CHANGE);
}
| digitalWrite(FRONT_PIN,LOW);//openforbusiness
| State=STATE_READY;
}

//SPIinterruptroutine
ISR(SPI_STC_vect){

valueIn=SPDR; //grabbytefromSPIDataRegister processIt=true;
}

voidIsrLeft()
{ //ISRforendofpulseonsonar10,11or12 isr1Count++;
noInterrupts();
SignalsReceived++;
if(digitalRead(IRQ2_PIN)==HIGH&&timeStartSet==false) {
timeStart=micros();
timeStartSet=true;
}
else
{
timeLeft=micros();
}
interrupts();
}
voidIsrBehind()
{ //ISRforendofpulseonsonar6or9 isr2Count++;
noInterrupts();
SignalsReceived++;
if(digitalRead(IRQ3_PIN)==HIGH&&timeStartSet==false) {
timeStart=micros();
timeStartSet=true;
}
else
{
timeBehind=micros();
}
interrupts();
}
voidIsrRight()
{//ISRforendofpulseonsonar1,2or3 //Logtimeofthepulseend
isr3Count++;
noInterrupts();
SignalsReceived++;
if(digitalRead(IRQ1_SCL_PIN)==HIGH&&timeStartSet==false) {
timeStart=micros();
timeStartSet=true;
}
else

{
timeRight=micros();
}
interrupts();
}

voidloop()
{
State=STATE_READY;
// | digitalWrite(RND0_PIN,LOW);
// | digitalWrite(RND1_PIN,LOW);
| setRound(0,0);
//readInput(); | //Sonarisslavewaitingforcommandfrommaster
//TODO:Sendstartsignaltorearboard.

//******Round1*******
State=STATE_ROUND1;
SignalsReceived=0;
//sendapulseonsonars
interrupts();
setRound(0,1);
// digitalWrite(RND1_PIN,HIGH);

timeoutStart=millis();
while(SignalsReceived<EXPECTED_SIGNALS1)
{
if((millis()-timeoutStart)>TIMEOUT_PERIOD)break; }
delay(ROUND_DELAY);
timeStartSet=false;
range[12]=(timeLeft-timeStart)/58; range[3] =(timeRight-timeStart)/58; range[9] =(timeBehind-timeStart)/58;

//******Round2*******
State=STATE_ROUND2;
SignalsReceived=0;
// | digitalWrite(RND0_PIN,HIGH);
// | sendapulseonsonars
| setRound(1,1);
| timeoutStart=millis();
| while(SignalsReceived<EXPECTED_SIGNALS2)
{

if((millis()-timeoutStart)>TIMEOUT_PERIOD)break; }
delay(ROUND_DELAY);
timeStartSet=false;
range[10]=(timeLeft-timeStart)/58; range[1] =(timeRight-timeStart)/58; range[6] =(timeBehind-timeStart)/58;

//******Round3*******
State=STATE_ROUND3;
// | digitalWrite(RND1_PIN,LOW);
| SignalsReceived=0;
| //sendapulseonsonars
| setRound(0,1);
| timeoutStart=millis();
| while(SignalsReceived<EXPECTED_SIGNALS3)
{
| if((millis()-timeoutStart)>TIMEOUT_PERIOD)break;
}
| delay(ROUND_DELAY);
| timeStartSet=false;
| range[2]=(timeLeft-timeStart)/58;
| range[11] =(timeRight-timeStart)/58;

// //TODO:Receivedatafromrearboard
| writeOutput();
| State=STATE_READY;
| roundCount++;
| //delay(120);
// | return;
}

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

digitalWrite(A3,LOW);
}elseif(highOrderBit==0&&lowOrderBit==1) {
//12,3,9
digitalWrite(A1,HIGH);
digitalWrite(A2,LOW);
digitalWrite(A3,LOW);
delay(10);
digitalWrite(A1,LOW);
}elseif(highOrderBit==1&&lowOrderBit==0) {
//2,11
digitalWrite(A1,LOW);
digitalWrite(A2,HIGH);
digitalWrite(A3,LOW);
delay(10);
digitalWrite(A2,LOW);
}elseif(highOrderBit==1&&lowOrderBit==1) {
//1,6,10
digitalWrite(A1,LOW);
digitalWrite(A2,LOW);
digitalWrite(A3,HIGH);
delay(10);
digitalWrite(A3,LOW);
}
}
voidreadInput()
{
byteselect;
//waitforhosttorequestinformation do
{
select=digitalRead(SNR_SEL_PIN);
}while(select==HIGH);
if(DEBUG)return;
while(!processIt||valueIn!=COMMAND_GO);//stayinroutineuntilcommandedto startonMOSI
processIt=false;
}

voidwriteOutput()
{
if(DEBUG){
if(VERBOSE_DEBUG){
Serial.print("Round:");
Serial.print(roundCount);
Serial.print("millis:");

Serial.print(millis());
Serial.print(",millissincelast:"); Serial.print(millis()-timeSinceLastRound); timeSinceLastRound=millis(); Serial.print(",SigReceived:"); Serial.print(SignalsReceived); Serial.print(",isr1:");
Serial.print(isr1Count);
Serial.print(",isr2:");
Serial.print(isr2Count);
Serial.print(",isr3:");
Serial.print(isr3Count);
Serial.print("Vals:");
}
for(inti=1;i<13;++i)
{
Serial.print(range[i]);
Serial.print("");
}
Serial.println();
}
else
{
//HereiswheredatawillbesentoverSPI.Stillneedswork intdataPos=0;
processIt=false;
while(dataPos<RANGE_DATA_SIZE){ inttimeStart=millis();
while(!processIt){
if(millis()-timeStart>TIMEOUT_PERIOD)break; }
writeIntData(range[dataPos++]);
delay(20);
}
dataPos=0;
}
}

//SendtwobytesoverSPIinordertorepresentanint voidwriteIntData(intdata)
{
bytehighOrderByte=(byte)(data>>8); bytelowOrderByte=(byte)data;

//Sendfirstbyte
SPDR=highOrderByte;
processIt=false;

//WaitforSPIinterruptbeforesedningsecondbyte while(!processIt)
{
if(millis()-timeStart>TIMEOUT_PERIOD)break; }
//Sendsecondbyte
SPDR=lowOrderByte;
processIt=false;
}

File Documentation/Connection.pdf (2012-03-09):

## Component interconnection

Anderson connector color code: Red: 36 V power or 36 V battery charge. Orange: 12 V power
Pink: 5 V power
Black: Ground
Green: Brake or Phase A or joystick center Blue: Throttle or Phase B
Yellow: Steer or Phase C

Hub motor

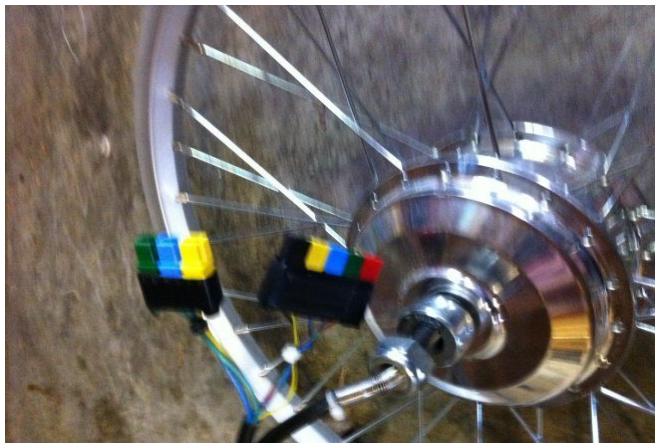
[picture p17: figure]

Original connections may be used, but have replaced with Anderson connectors for better robustness.

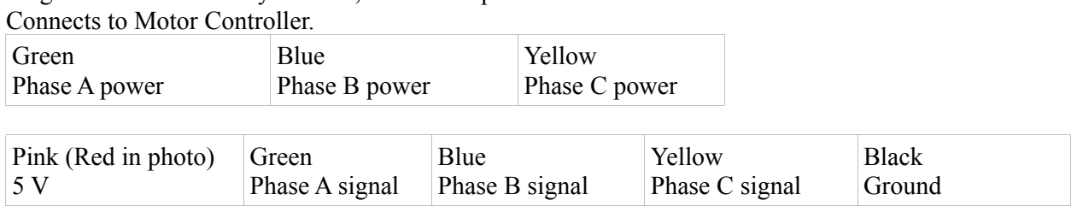
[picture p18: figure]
Connects to Motor Controller. Green Phase A power; Blue Phase B power; Yellow Phase C power; Pink (Red in photo) 5 V; Green Phase A signal; Blue Phase B signal; Yellow Phase C signal; Black Ground

Motor Controller
Connects to Hub motor
Green
Phase A power

Blue
Phase B power

Yellow
Phase C power

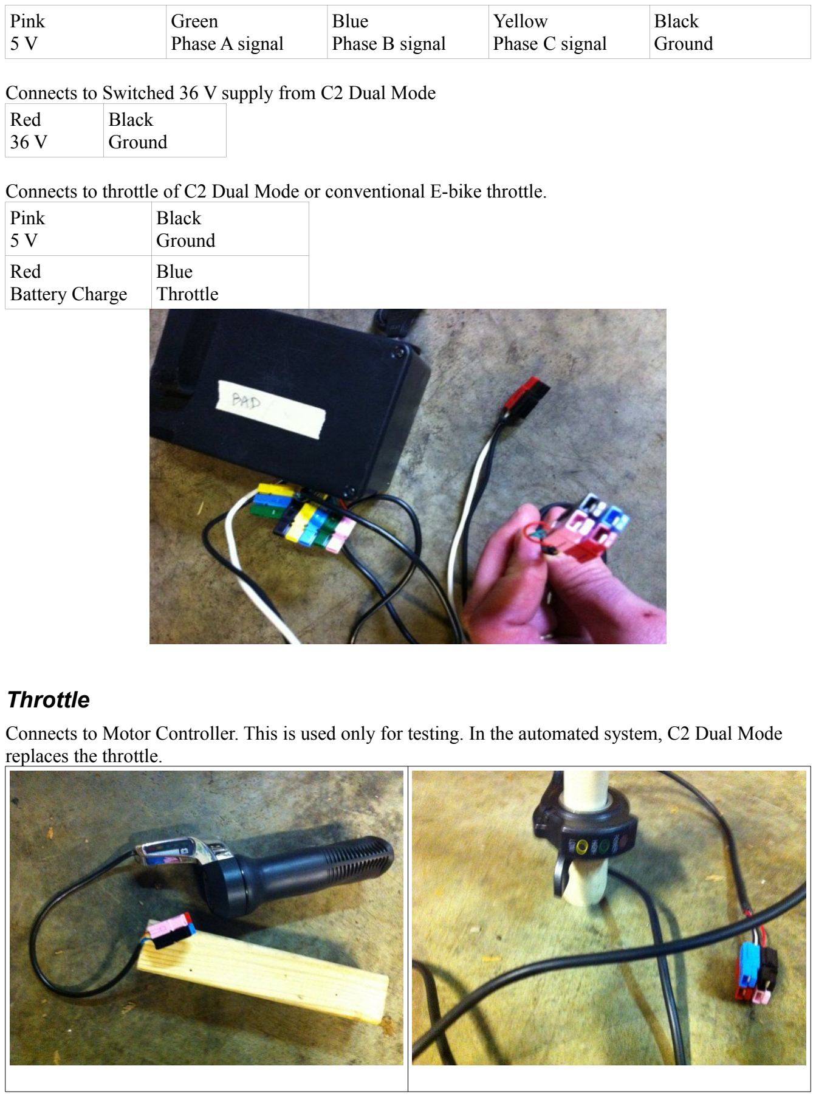
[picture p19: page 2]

Pink
5 V

Green
Phase A signal

Blue
Phase B signal

Yellow
Phase C signal

Black
Ground

Connects to Switched 36 V supply from C2 Dual Mode Red
36 V

Black
Ground

Connects to throttle of C2 Dual Mode or conventional E-bike throttle. Pink
5 V

Black
Ground
Red
Battery Charge

Blue
Throttle

Throttle
Connects to Motor Controller. This is used only for testing. In the automated system, C2 Dual Mode replaces the throttle.

Red
Battery Charge

Blue
Throttle
Pink
5 V

Black
Ground

Joystick

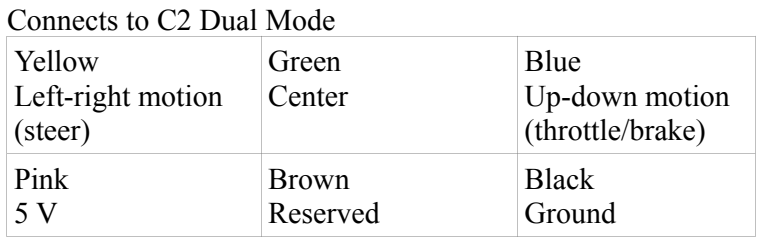
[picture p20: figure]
Connects to C2 Dual Mode Yellow Left-right motion (steer); Green Center; Blue Up-down motion (throttle/brake); Pink 5 V; Brown Reserved; Black Ground

## C2 Dual Mode

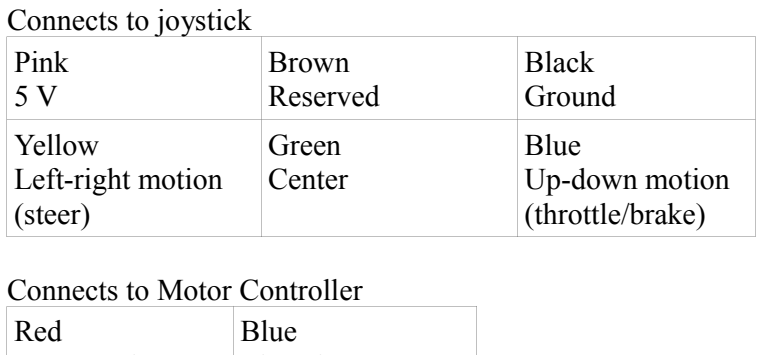
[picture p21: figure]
Connects to joystick Pink 5 V; Brown Reserved; Black Ground; Yellow Left-right motion (steer); Green Center; Blue Up-down motion (throttle/brake); Connects to Motor Controller Red; Blue

Battery Charge

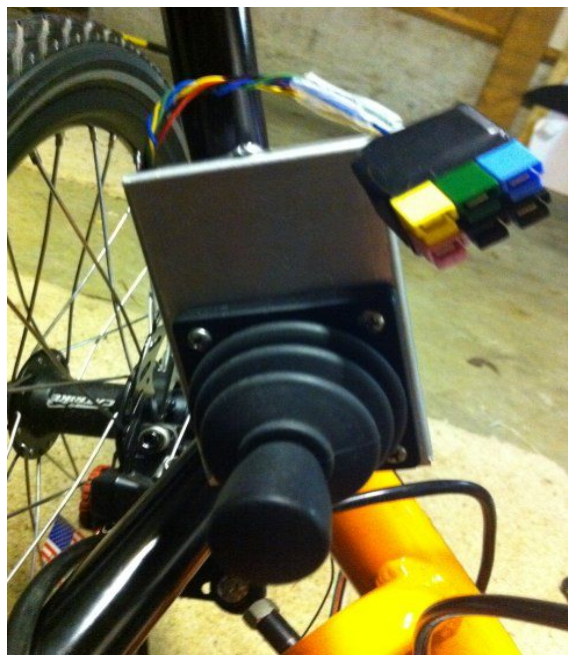
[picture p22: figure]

Throttle

Pink
5 V

Black
Ground

Connects to Motor Controller Red
36 V

Black
Ground

Connects to Battery
Red
36 V

Black
Ground

Orange
12 V

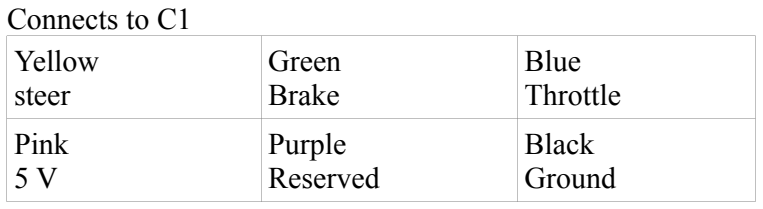
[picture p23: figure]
Connects to C1 Yellow steer; Green Brake; Blue Throttle; Pink 5 V; Purple Reserved; Black Ground
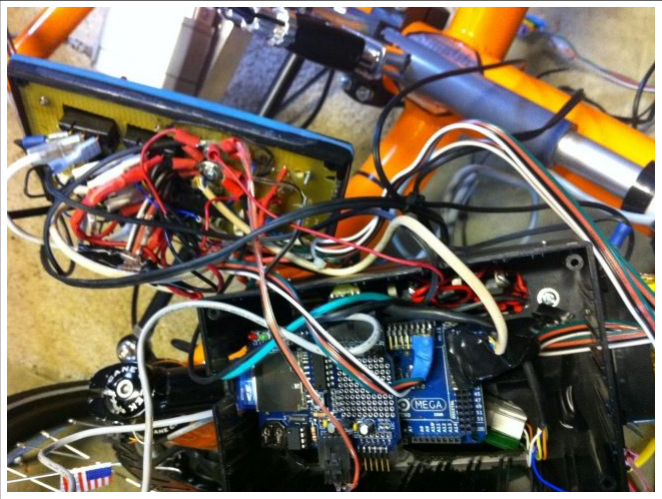
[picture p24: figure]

Front panel switches:

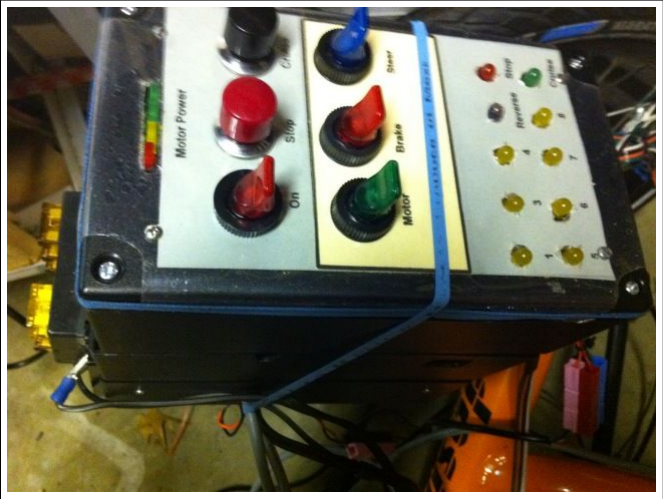
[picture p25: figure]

On: Turns on 5V, 12V and 36V power. 36V power also requires key switch on motor controller. Stop: Momentary switch; may also be activated wirelessly.
Cruise: Momentary switch; may also be activated wirelessly.
Motor: Enables computer control of motor; when off, motor is controlled by joystick.
Brake: Enables computer control of brakes; when off, brakes are controlled by joystick. Steer: Enables computer control of steering; when off, steering is controlled by joystick.
Top LEDs show battery charge.
Ten lower LEDs include internal Stop and Cruise that match the switch state. An LED marked “Reverse” is reserved. The other 7 LEDs may either come internally from C2 or externally from other microprocessors.

LED input connections are:
Green: 4 | Blue: 3 | Purple: 1


Yellow: 5 | Brown: 6 | Gray: 7 | White: 8

LED output connections are:
Yellow: 5 | Brown: 6 | Gray: 7 | White: 8
| Green: 4 | Blue: 3 | Purple: 1

Servos

The brake servo pushes a brake lever that connects to disk brakes on the left and right wheels. The pusher is a slotted PVC tube designed so that the rider can use the lever as an emergency brake. Brake lever and servo are between the rider's legs.
Steering servo is linked to the tie bar connecting the front wheels. It is under the seat.
Both servos are cabled directly to controllers inside the C2 box.
C1 and C3 Pilot
This is the lowest level of computer control.

Connects to C2 Pink 5 V; Purple Reserved; Black Ground; Yellow steer; Green Brake; Blue Throttle

C6 Navigator
Contains shield with GPS logger and SD card.


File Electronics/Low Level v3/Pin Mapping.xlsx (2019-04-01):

Mega2560 Pin Number | Mega2560 Pin Name | Arduino Pin Name | Second Draft LLBV3 Pin Name | LLBV3 Header / Function
1 | PG5 ( OC0B ) | Digital pin 4 (PWM)
2 | PE0 ( RXD0/PCINT8 ) | Digital pin 0 (RX0) | RX0 | USB Serial
3 | PE1 ( TXD0 ) | Digital pin 1 (TX0) | TX0 | USB Serial
4 | PE2 ( XCK0/AIN0 )
5 | PE3 ( OC3A/AIN1 ) | Digital pin 5 (PWM) | WATCHDOG | X3, for power on board
6 | PE4 ( OC3B/INT4 ) | Digital pin 2 (PWM) | Brake_PWM | X3, for power on board
7 | PE5 ( OC3C/INT5 ) | Digital pin 3 (PWM)
8 | PE6 ( T3/INT6 )
9 | PE7 ( CLKO/ICP3/INT7 )
10 | VCC | VCC
11 | GND | GND
12 | PH0 ( RXD2 ) | Digital pin 17 (RX2)
13 | PH1 ( TXD2 ) | Digital pin 16 (TX2)
14 | PH2 ( XCK2 )
15 | PH3 ( OC4A ) | Digital pin 6 (PWM)
16 | PH4 ( OC4B ) | Digital pin 7 (PWM) | STEER_SERVO_PWM | Steering header
17 | PH5 ( OC4C ) | Digital pin 8 (PWM)
18 | PH6 ( OC2B ) | Digital pin 9 (PWM)
19 | PB0 ( SS/PCINT0 ) | Digital pin 53 (SS) | SPI_SLAVE | SPI header (this pin tells the mega to be a slave)
20 | PB1 ( SCK/PCINT1 ) | Digital pin 52 (SCK) | SCK | all SPI devices, SPI header
21 | PB2 ( MOSI/PCINT2 ) | Digital pin 51 (MOSI) | MOSI | all SPI devices, SPI header
22 | PB3 ( MISO/PCINT3 ) | Digital pin 50 (MISO) | MISO | all SPI devices, SPI header
23 | PB4 ( OC2A/PCINT4 ) | Digital pin 10 (PWM)
24 | PB5 ( OC1A/PCINT5 ) | Digital pin 11 (PWM)
25 | PB6 ( OC1B/PCINT6 ) | Digital pin 12 (PWM)
26 | PB7 ( OC0A/OC1C/PCINT7 ) | Digital pin 13 (PWM)
27 | PH7 ( T4 )
28 | PG3 ( TOSC2 )
29 | PG4 ( TOSC1 )
30 | RESET | RESET
31 | VCC | VCC
32 | GND | GND
33 | XTAL2 | XTAL2
34 | XTAL1 | XTAL1
35 | PL0 ( ICP4 ) | Digital pin 49 | CAN_SS | MCP2515 slave selection
36 | PL1 ( ICP5 ) | Digital pin 48 | DAC_SS | DAC slave selection
37 | PL2 ( T5 ) | Digital pin 47
38 | PL3 ( OC5A ) | Digital pin 46 (PWM)
39 | PL4 ( OC5B ) | Digital pin 45 (PWM)
40 | PL5 ( OC5C ) | Digital pin 44 (PWM)
41 | PL6 | Digital pin 43
42 | PL7 | Digital pin 42
43 | PD0 ( SCL/INT0 ) | Digital pin 21 (SCL)
44 | PD1 ( SDA/INT1 ) | Digital pin 20 (SDA)
45 | PD2 ( RXDI/INT2 ) | Digital pin 19 (RX1)
46 | PD3 ( TXD1/INT3 ) | Digital pin 18 (TX1)
47 | PD4 ( ICP1 )
48 | PD5 ( XCK1 )
49 | PD6 ( T1 )
50 | PD7 ( T0 ) | Digital pin 38
51 | PG0 ( WR ) | Digital pin 41 | BRAKE_ON | on-board relay
52 | PG1 ( RD ) | Digital pin 40 | BUZZER | on-board buzzer
53 | PC0 ( A8 ) | Digital pin 37 | VOLTAGE_SWITCH | on-board relay
54 | PC1 ( A9 ) | Digital pin 36 | D_36 | X3, no purpose assgined
55 | PC2 ( A10 ) | Digital pin 35
56 | PC3 ( A11 ) | Digital pin 34 | FWDSW | X3, for power on board
57 | PC4 ( A12 ) | Digital pin 33
58 | PC5 ( A13 ) | Digital pin 32
59 | PC6 ( A14 ) | Digital pin 31
60 | PC7 ( A15 ) | Digital pin 30
61 | VCC | VCC
62 | GND | GND
63 | PJ0 ( RXD3/PCINT9 ) | Digital pin 15 (RX3) | RX3 | X3, for power on board
64 | PJ1 ( TXD3/PCINT10 ) | Digital pin 14 (TX3) | TX3 | X3, for power on board
65 | PJ2 ( XCK3/PCINT11 )
66 | PJ3 ( PCINT12 )
67 | PJ4 ( PCINT13 )
68 | PJ5 ( PCINT14 )
69 | PJ6 ( PCINT 15 )
70 | PG2 ( ALE ) | Digital pin 39
71 | PA7 ( AD7 ) | Digital pin 29
72 | PA6 ( AD6 ) | Digital pin 28
73 | PA5 ( AD5 ) | Digital pin 27
74 | PA4 ( AD4 ) | Digital pin 26
75 | PA3 ( AD3 ) | Digital pin 25
76 | PA2 ( AD2 ) | Digital pin 24 | REVERSE | X3, for power on board
77 | PA1 ( AD1 ) | Digital pin 23
78 | PA0 ( AD0 ) | Digital pin 22 | REGEN_ACTIVE | X3, for power on board
79 | PJ7
80 | VCC | VCC
81 | GND | GND
82 | PK7 ( ADC15/PCINT23 ) | Analog pin 15 | HALLPHASEA (INT) | X3, for power on board
83 | PK6 ( ADC14/PCINT22 ) | Analog pin 14 | HALLPHASEB (INT) | X3, for power on board
84 | PK5 ( ADC13/PCINT21 ) | Analog pin 13 | EBIKECONTRL (INT) | X3, for power on board
85 | PK4 ( ADC12/PCINT20 ) | Analog pin 12 | HALLPHASEC (INT) | X3, for power on board
86 | PK3 ( ADC11/PCINT19 ) | Analog pin 11 | Speedometer (INT) | X3, for power on board
87 | PK2 ( ADC10/PCINT18 ) | Analog pin 10 | CAN_INT | MCP 2515 interrupt on received frames
88 | PK1 ( ADC9/PCINT17 ) | Analog pin 9 | E-stop (INT) | E-stop jumper, also X3
89 | PK0 ( ADC8/PCINT16 ) | Analog pin 8 | Wheel Rotation (INT) | wheel hall switch header
90 | PF7 ( ADC7 ) | Analog pin 7 | R_RTN_GND | Steering header
91 | PF6 ( ADC6 ) | Analog pin 6 | L_RTN_GND | Steering header
92 | PF5 ( ADC5/TMS ) | Analog pin 5
93 | PF4 ( ADC4/TMK ) | Analog pin 4
94 | PF3 ( ADC3 ) | Analog pin 3 | R_SENSE | Steering header
95 | PF2 ( ADC2 ) | Analog pin 2 | L_SENSE | Steering header
96 | PF1 ( ADC1 ) | Analog pin 1
97 | PF0 ( ADC0 ) | Analog pin 0
98 | AREF | Analog Reference
99 | GND | GND
100 | AVCC | VCC

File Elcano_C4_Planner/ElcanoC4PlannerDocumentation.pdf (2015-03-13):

# Elcano C4 Planner Documentation

## Getting Started With C4 Planner

Before you can use the Elcano C4 Planner, you need to follow these steps. If you've already downloaded all of the Elcano files and imported all of the libraries, you can skip these steps.

### 1. Clone the Elcano repository

Go to https://github.com/elcano/elcano and use your preferred method to clone the repository. For example, if you want to clone it using https, you would select "HTTPS" on the righthand side, click "Copy to clipboard," and paste it into your git interface.

If you're using Git Bash, you would type in:

$gitclonehttps://github.com/elcano/elcano.git

### 2. Open the C4 Planner file

From the Arduino IDE, select File > Open and navigate to \elcano\Elcano_C4_Planner\Elcano_C4_Planner.ino

### 3. Add the Elcano libraries

In the Arduino IDE, select Sketch > Import Library > Add Library. Navigate to \elcano\libraries\Common. Repeat for \elcano\libraries\IO. These are the minimum required for C4 Planner, though you may want to import the rest if you will be working with other Elcano files.

Once the repository is cloned and the libraries are added you should be able to compile the C4 planner .ino file.

## Elcano C4 Planner File System

### MAP_DEFS.TXT

This file provides the latitude and longitude coordinates for each of the maps, followed by the file name for that map. Commas also separate each map.

The format should be as follows:

latitude_0,longitude_0,filename_0.txt, ...,
latitude_n,longitude_n,filename_n.txt

A practical example would look like this:

47.758949,-122.190746,MAP001.txt, 47.6213,-122.3509,MAP002.txt

### Map Files

These files provide the junction data. The junction struct has the following variables:

long east_mm
long north_mm
int destination[4]
long Distance[4]
- east_mm is the position East of the origin in millimeters
- north_mm is the position North of the origin in millimeters
- destination is an array of indeces into the Nodes[] array that connect to this node
- Distance is an array of longs holding the distances from this node to each of the destinations in millimeters.

The file format is a comma delimited list of the values in the struct, with a comma after each junction. It should be formatted as follows:

east_mm_0,north_mm_0,destination_0[0],destination_0[1],destination_0[2],des tination_0[3],Distance_0[0],Distance_0[1],Distance_0[2],Distance_0[3], ...,
east_mm_n,north_mm_n,destination_n[0],destination_n[1],destination_n[2],des tination_n[3],Distance_n[0],Distance_n[1],Distance_n[2],Distance_n[3],

A practical example would look like this:

-183969,380865,1,2,END,END,1,1,1,1, -73039,380865,0,3,7,END,1,1,1,1, -182101,338388,0,3,4,5,1,1,1,1

### File Names

The Arduino SD Card library uses a FAT file system. FAT file systems have a limitation when it comes to naming conventions. You must use the 8.3 format, so that file names look like “NAME001.EXT”, where “NAME001” is an 8 character or fewer string, and “EXT” is a 3 character extension. People commonly use the extensions .TXT and .LOG. It is possible to have a shorter file name (for example, mydata.txt, or time.log), but you cannot use longer file names.

## Elcano C4 Planner Code Descriptions

Initial position. Specifies the starting location and orientation. Velocity is zero. If this is a file, it is read by C4 (Path Planner) and passed to C6 (Navigator). If it is user input, it is read by C6 (Navigator).

The present C4 module is the only microcontroller that has a file system.

USB: All Arduinos contain a USB port that lets them download code from a PC.
Since a USB connection is not a network, the Arduinos cannot talk to each other over USB. To enable USB, one of the Arduinos must include a USB server. If there is a USB server, it might be
C4, which may have an OS, or
C6, which needs to talk to lots of instruments, or
C7, which may have a USB link to a camera, or
we could have another processor whose sole function is communication.

Nodes and Linksdefine the road network.
The path for the robot is an array of pointers to Nodes.
LATITUDE_ORIGIN and LONGITUDE_ORIGIN define (0,0) on the mm coordinate system. Startis the position of the robot as it begins a new leg of the journey.
Destinationis the next goal position in mission.
Pathjoins Start and Destination. Finding it is the major task of this Path Planner module. The Distancenumbers are initially multipliers giving path roughness.
They are replaced by their product with the actual distance.
Routeis a finer scale list of waypoints from present or recent position.
Exitis the route from Path[last]> location to Destination.

### Functions and data

Defines
PI ((float) 3.1415925)
NULL 0
START -1
EMPTY -2
CONES 5
DESIRED_SPEED_mmPs 2235 // == 5mph, conversion chart in file MAX_WAYPOINTS 40

MAX_MAPS 10

void DataReady(); | //an interrupt is attached to this in the setup, must be
implemented
extern bool DataAvailable; //TODO: implement this bool and the above function

Goals
These are hardcoded POIs that make up the planned route

long goal_lat[CONES] = { 47621881, 47621825, 47623144, 47620616, 47621881}; long goal_lon[CONES] = {-122349894, -122352120, -122351987, -122351087, -122349894};

struct curve Links[20]; | // the links between junctions
struct junction Nodes[MAP_POINTS] | // the hardcoded lat&long, nodes pointed to, and
// cost multipliers for each junction node struct AStar
{
int ParentID;
long CostFromStart;
long CostToGoal;
long TotalCost;
} Open[MAP_POINTS]; // list used in A* to meant to track unvisited nodes

class waypoint Origin, Start;
waypoint Path[MAX_WAYPOINTS]; | // course route to goal
waypoint FinePath[MAX_WAYPOINTS]; | // a low level part of path that smoothes the
corners.
waypoint mission[CONES]; | // aka MDF
int waypoints = CONES;

void ConstructNetwork(junction *Map, int MapPoints)
Takes an array of junctions (intersections) and an integer representing the number of junctions in the array as input. Calculates the distance for all of the edges in the junction and updates the distance value from the multiplier value the array is created with to the distance in mm.

void GetGoals(waypoint *Waypoint, int Goals)

Takes the Mission waypoint array and constructs the Goals array for building the path to take. Currently does not use the *Waypoint or Goals arguments, and instead uses the global Mission and Goals arrays. Can be updated to use the arguments passed in or to remove the arguments if needed.
long distance(int i, int *k, long east_mm, long north_mm, int* perCent)
Takes the Nodes index (i), a pointer to an index (*k), the east and north coordinates in millimeters, and the percentage of the segment completed and calculates the distance. This is used by the FindClosestRoad function.

void FindClosestRoad(waypoint *start, waypoint *road)
Takes two waypoints, finds the closest junction to the first waypoint and points the second waypoint to that junction. For example, if your map has junctions at (1,1), (-1,1), (1, -1), and (-1,-1) and you pass in your starting waypoint as (2,2), the road waypoint will be updated to (1,1), which is the closest junction to (2,2).

int BuildPath (int j, waypoint* start, waypoint* destination)
int FindPath(waypoint *start, waypoint *destination)
int PlanPath (waypoint *start, waypoint *destination)
These three functions work together to implement the A* pathing. They take in start and destination waypoints which are on the road network given in Nodes and set the waypoints on the path starting with Start and ending with Destination. A* is traditionally done with pushing and popping node from an Open and Closed list. However, since we have a small number of nodes, we instead reserve a slot on global variables Open and Closed for each node.

void SendPath(waypoint *course, int count)
Sends the path to the C3 pilot module via Serial bus.

boolean LoadMap(char* fileName)
The LoadMap function loads the map nodes from a file. It takes in the name of the file to load and loads the appropriate map. LoadMap returns true if the map was loaded. It returns false if the load failed.

void SelectMap(waypoint currentLocation, char* fileName, char* nearestMap)
The SelectMap function determines which map to load. It does this by taking in the current location as a waypoint and a string with the name of the file that contains the origins and file names of the maps. The function then determines which origin is closest to the waypoint and returns the filename as a string. It assumes that the file is formatted according to the specifications.

void initialize()
Initializes the Origin, reads the map definitions from SD, loads the appropriate map file, and builds the desired path based on the mission files.

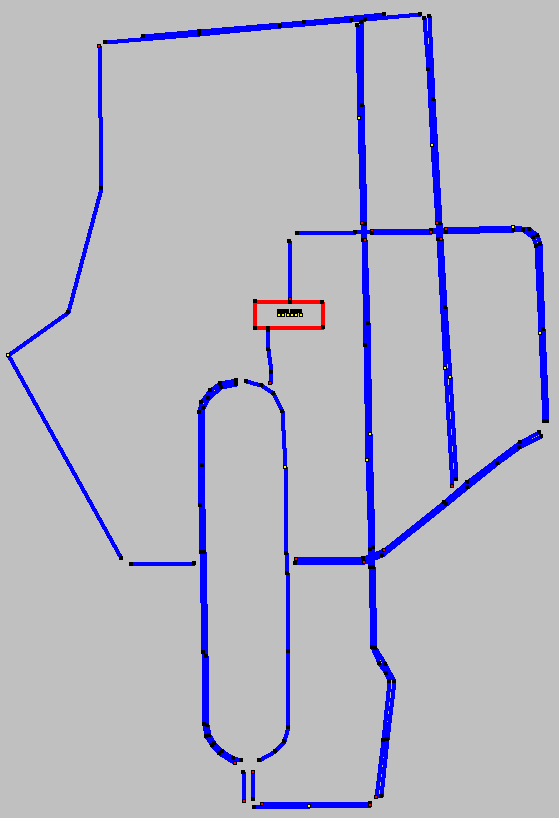
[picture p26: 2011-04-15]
RNDF/Sample_RNDF.png

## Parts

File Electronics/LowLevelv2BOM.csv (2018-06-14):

Part | Value | Device | Package | Description | MF | MPN | OC_FARNELL | OC_NEWARK
ADCH | Analog In 8-15 | PINHD-1X8 | 1X08 | PIN HEADER
ADCL | Analog In 0-7 | PINHD-1X8 | 1X08 | PIN HEADER
C1 | 0.1uF | C-US025-025X050 | C025-025X050 | CAPACITOR, American symbol
C2 | 0.1uF | C-US025-025X050 | C025-025X050 | CAPACITOR, American symbol
C3 | 1 uF | C-US025-030X050 | C025-030X050 | CAPACITOR, American symbol
C4 | 1 uF | C-US025-030X050 | C025-030X050 | CAPACITOR, American symbol
C5 | 1 uF | C-US025-030X050 | C025-030X050 | CAPACITOR, American symbol
C6 | 0.1uF | C2.5/2 | C2.5-2 | CAPACITOR
C7 | 0.1uF | C2.5/2 | C2.5-2 | CAPACITOR
C8 | 1 uF | C-US025-030X050 | C025-030X050 | CAPACITOR, American symbol
C9 | 1 uF | C-US025-030X050 | C025-030X050 | CAPACITOR, American symbol
C10 | 1 uF | C-US025-030X050 | C025-030X050 | CAPACITOR, American symbol
COMM_DIG | DIG 14-21 | PINHD-1X8 | 1X08 | PIN HEADER
D8-13 | PWMH | PINHD-1X8 | 1X08 | PIN HEADER
GND | GND | PINHD-1X1 | 1X01 | PIN HEADER
IC1 | DS 8291 | DIL8 | DIL08 | Dual In Line / Socket
IC2 | MCP4802 | DIL8 | DIL08 | Dual In Line / Socket
IC3 | MCP4802 | DIL8 | DIL08 | Dual In Line / Socket
IC4 | DS 8291 | DIL8 | DIL08 | Dual In Line / Socket
ICSP | ICSP | PINHD-2X3 | 2X03 | PIN HEADER
JP1 | 5V | PINHD-1X1 | 1X01 | PIN HEADER
JP2 | 5V | PINHD-1X1 | 1X01 | PIN HEADER
JP3 | GND | PINHD-1X1 | 1X01 | PIN HEADER
JP5 | Left | PINHD-1X4/90 | 1X04/90 | PIN HEADER
JP6 | Right | PINHD-1X4/90 | 1X04/90 | PIN HEADER
JP7 |  | PINHD-1X7 | 1X07 | PIN HEADER
JP8 |  | PINHD-2X7 | 2X07 | PIN HEADER
JP9 | Joystick | PINHD-1X8/90 | 1X08/90 | PIN HEADER
JP10 |  | JP1E | JP1 | JUMPER
JP11 | Brake Servo | PINHD-1X3/90 | 1X03/90 | PIN HEADER
JP12 | Steer Servo | PINHD-1X3/90 | 1X03/90 | PIN HEADER
JP13 |  | JP1E | JP1 | JUMPER
POWER | POWER | PINHD-1X6 | 1X06 | PIN HEADER
PWML | Digital 0-7 | PINHD-1X8 | 1X08 | PIN HEADER
R1 | 1M | R-US_0207/10 | 0207/10 | RESISTOR, American symbol
R2 | 10M | R-US_0207/10 | 0207/10 | RESISTOR, American symbol
R3 | 4.7 K | R-US_0207/10 | 0207/10 | RESISTOR, American symbol
R4 | 4.7 K | R-US_0207/10 | 0207/10 | RESISTOR, American symbol
R6 | 4.7 K | R-US_0207/10 | 0207/10 | RESISTOR, American symbol
R7 | 100 | R-US_0207/10 | 0207/10 | RESISTOR, American symbol
R8 | 4.7 K | R-US_0207/10 | 0207/10 | RESISTOR, American symbol
R9 | 4.7 K | R-US_0207/10 | 0207/10 | RESISTOR, American symbol
R10 | 4.7 K | R-US_0207/10 | 0207/10 | RESISTOR, American symbol
R11 | 100 | R-US_0207/10 | 0207/10 | RESISTOR, American symbol
U$1 | DPDT_DEV6X5MM_PAC | DPDT_DEV6X5MM_PAC | NEWSWITCH2_PAC
U$2 | CUI_JACKTHROUGH_HOLE | CUI_JACKTHROUGH_HOLE | CUIJACK
X1 | RJ45-8L-B | RJ45-8L-B | RJ45-NO-SHIELD | CORCOM Modular RJ Jacks No Shield | TYCO ELECTRONICS | RJ45-8L-B | 1279843 | 52K4445
X2 | Cruise | F25H | F25H | SUB-D |  |  | unknown | unknown
X3 | Motor | M15-182 | 182-015-MALE | SUB-D |  |  | unknown | unknown
X4 | CLICK | ODO_JACK | ODO_JACK
X5 | RJ45-8L-B | RJ45-8L-B | RJ45-NO-SHIELD | CORCOM Modular RJ Jacks No Shield | TYCO ELECTRONICS | RJ45-8L-B | 1279843 | 52K4445
XIOH | Digital 22-37 | PINHD-2X8 | 2X08 | PIN HEADER
XIOL | Digital 38-53 | PINHD-2X8 | 2X08 | PIN HEADER

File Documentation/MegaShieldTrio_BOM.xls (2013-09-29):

Trio board |  | Bill of Materials |  | 9/10/13
Part | Where | Quantity | Appox price | Extended | Manufacturer | M Part # | Source | Supplier part # | Link
MegaShieldTrio PCB |  | 1 | 13.00 | 13.00 | ElcanoProject | Trio-PCB
Relay | RL1 | 1 | 2.57 | 2.57 | TE Connectivity | TSC-105D3H,000 | DigiKey | PB1016-ND | http://www.digikey.com/product-search/en?WT.z_header=search_go&lang=en&site=us&x=12&y=12&formaction=on
1X7HEADER | C3,C4 | 4 | 0.62 | 2.48 | FCI | 71920-407LF | Mouser | 649-71920-407LF
1x10 Header | Mouse | 1 | 1.11 | 1.11 | FCI | 75915-310LF | Mouser | 649-75915-310LF
1x9 Header | CHRUM6 | 1 | 0.89 | 0.89 | FCI | 75915-409LF | Mouser | 649-75915-409LF
1X8HEADER | C4SD0-13,C3,C4 | 6 | 0.84 | 5.04 | FCI | 75915-308LF | Mouser | 649-75915-308LF
1X6HEADER | C4SPwr,C4SA | 2 | 0.71 | 1.42 | FCI | 75915-306LF | Mouser | 649-75915-306LF
1x2 Header | CHRUM6 | 2 | 0.30 | 0.60 | FCI | 75915-302LF | Mouser | 649-75915-302LF
1x8 Stack Header | D0-13,A0-7 | 3 |  | 1.76 |  |  | Pololu | 1035 | http://www.pololu.com/catalog/product/1035
1x6 Stack Header | Power | 1 |  |  |  |  | Pololu | 1035
1x8 M pins | D14-21,A8-15 | 2 | 0.22 | 0.44 | FCI | 68000-408HLF | DigiKey | 609-3264-ND | http://www.digikey.com/product-search/en?WT.z_header=search_go&lang=en&site=us&x=11&y=14&formaction=on
2x15 M pins | D28-53 | 1 | 0.53 | 0.53 | Sullins Connector | PREC015DAAN-RC | DigiKey | S2012EC-15-ND | http://www.digikey.com/product-detail/en/PREC015DAAN-RC/S2012EC-15-ND/2774879
1x2 M pins | D23,25 | 1 | 0.10 | 0.10 | Sullins Connector | PREC002SAAN-RC | DigiKey | S1012EC-02-ND | http://www.digikey.com/product-detail/en/PREC002SAAN-RC/S1012EC-02-ND/2774852
1x3 M pins | D22,24,26 | 1 | 0.11 | 0.11 | Sullins Connector | PREC003SAAN-RC | DigiKey | S1012EC-03-ND | http://www.digikey.com/product-detail/en/PREC003SAAN-RC/S1012EC-03-ND/2774851
ODO_JACK | X2,X3 | 2 | 0.53 | 1.06 | CUI Inc | MJ1-2503A | DigiKey | CP1-2503AM-ND | http://www.digikey.com/product-search/en?WT.z_header=search_go&lang=en&site=us&x=18&y=15&formaction=on
RJ45-8L-B | X4,X5 | 2 | 0.48 | 0.96 | FCI | 54602-908LF | DigiKey | 609-1046-ND | http://www.digikey.com/product-search/en?WT.z_header=search_go&lang=en&site=us&x=17&y=17&formaction=on
M25 SubD connector | X1 | 1 | 1.18 | 1.18 | FCI | 10090097-P254VLF | DigiKey | 609-4006-ND | http://www.digikey.com/product-search/en?WT.z_header=search_go&lang=en&site=us&x=11&y=16&formaction=on
Resistor 1 M | R1,R2,R3 | 3 | 0.03 | 0.09 | Stackpole Electronics | CF14JT1M00 | DigiKey | CF14JT1M00CT-ND | http://www.digikey.com/product-detail/en/CF14JT1M00/CF14JT1M00CT-ND/1830423
2x3 M pins | ICSP | 1 | 0.22 | 0.22 | Sullins Connector | PREC003DAAN-RC | DigiKey | S2012EC-03-ND | http://www.digikey.com/product-detail/en/PREC003DAAN-RC/S2012EC-03-ND/2774891
Parts TOTAL |  |  |  | 33.56
Price |  |  |  | 90.00
Purchased separately
Arduino Mega 2560 |  | 1 | 55.13 | 55.13 | Arduino |  | Robot Shop | RB-Ard-33
Arduino Nano |  | 2 | 34.99 | 69.98 |  |  | Robot Shop | RB-Gra-01
GPS Log Shield |  | 1 | 50 | 50.00 |  |  | Adafruit | 1272 | http://www.adafruit.com/products/1272
SD Shield |  | 1 | 20 | 20.00 |  |  | Adafruit | 1141 | http://www.adafruit.com/products/1141
Micro SD Card |  | 1 | 7 | 7.00 | Kingston |  | Amazon |  | http://www.amazon.com/Kingston-microSDHC-Memory-SDC4-8GBET/dp/B00200K1TS
SD Card |  | 1 | 9 | 9.00 | Transcend |  | Amazon |  | http://www.amazon.com/Transcend-Class-Flash-Memory-TS8GSDHC10E/dp/B003VNKNEG
UM-6 LT Orientation sensor |  | 1 | 149 | 149.00 |  |  | Pololu | 1256 | http://www.pololu.com/catalog/product/1256
DB-25 Cable M-F |  | 1 | 6.76 | 6.76 | Assmann WSW | AK135-2-R | DigiKey | AE9865-ND | http://www.digikey.com/product-detail/en/AK135-2-R/AE9865-ND/821620
Ethernet Cable |  | 1 | 2.19 | 2.19 | Assmann WSW Comp | DK-1511-003/B | DigiKey | AE10481-ND | http://www.digikey.com/product-detail/en/DK-1511-003%2FB/AE10481-ND/2268273
Cable |  | 1 | 2.57 | 2.57 | Tensility Inrtnl | CA-2201 | DigiKey | CP-2201-ND | http://www.digikey.com/product-search/en?WT.z_header=search_go&lang=en&site=us&x=11&y=15&formaction=on
9.6V Battery & charger |  | 1 | 24 | 24.00 | Nitro Power |  | BatteryMart | RC-R96K | http://www.batterymart.com/p-rc-r96k-nitropower-battery-and-charger.html?device=c&network=g&matchtype=
Battery Connector |  | 1 |  | 0.00
Optical mouse odometer |  | 1 | 35 | 35.00
TOTAL |  |  |  | 430.63
Grand total |  |  |  | 520.63

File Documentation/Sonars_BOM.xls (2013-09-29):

Sonars board | Bill of Materials |  | 9/10/13
Part | Quantity | Appox price | Extended | Manufacturer | M Part # | Source | Supplier part # | Link
Sonars PCB | 1 | 6.00 | 6.00 | ElcanoProject | Sonar-PCB
RJ45-8L-B | 1 | 0.48 | 0.48 | FCI | 54602-908LF | DigiKey | 609-1046-ND | http://www.digikey.com/product-search/en?WT.z_header=search_go&lang=en&site=us&x=17&y=17&formaction=on
1x7 Socket | 5 | 0.62 | 3.10 | FCI | 71920-407LF | Mouser | 649-71920-407LF
7x1 Angled pins | 5 | 0.62 | 3.10 | Molex | 22288073 | DigiKey | WM50026-07-ND | http://www.digikey.com/product-search/en?WT.z_header=search_go&lang=en&site=us&x=18&y=14&formaction=on
Sonar mounts | 5 | 1.50 | 7.50 | ElcanoProject | Sonar-MNT
Machine screw 4-40 | 5 | 0.03 | 0.15 | B&F Fastener Supply | PMS 440 0075 PH | DigiKey | H350-ND | http://www.digikey.com/product-search/en/hardware-fasteners-accessories/screws-bolts/2097339?k=H350-ND
Hex nut 1/14” 4-40 | 5 | 0.02 | 0.10 | B&F Fastener Supply | HNZ 440 | DigiKey | H216-ND | http://www.digikey.com/product-search/en?WT.z_header=search_go&lang=en&site=us&x=16&y=13&formaction=on
Parts TOTAL |  |  | 20.43
Price |  |  | 80.00
Purchased separately
Maxbotix XL-MaxSonar EZ0, EZ2 or EZ4 | 5 | 45.00 | 225.00 | Maxbotix | MB-1202 | Pololu | 1650 | http://www.maxbotix.com/Ultrasonic_Sensors/MB1202.htm
Ethernet cable | 1 | 2.19 | 2.19 | Assmann WSW Comp | DK-1511-003/B | DigiKey | AE10481-ND | http://www.digikey.com/product-detail/en/DK-1511-003%2FB/AE10481-ND/2268273
TOTAL |  |  | 227.19
Grand total |  |  | 307.19

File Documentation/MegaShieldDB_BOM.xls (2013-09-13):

DB board | Bill of Materials |  | 9/11/13
Part | Where | Quantity | Appox price | Extended | Manufacturer | M Part # | Source | Supplier part # | Link
MegaShieldDB PCB |  | 1 | 40.00 | 40.00 | ElcanoProject | DB-PCBv1
1x8 Stack Header | D0-13,A0-7 | 3 |  | 1.76 |  |  | Pololu | 1035 | http://www.pololu.com/catalog/product/1035
1x6 Stack Header | Power | 1 |  |  |  |  | Pololu | 1035
1x8 M Hdr .23 | D14-21,A8-15 | 2 | 0.22 | 0.44 | FCI | 68000-408HLF | DigiKey | 609-3264-ND | http://www.digikey.com/product-search/en?WT.z_header=search_go&lang=en&site=us&x=11&y=14&formaction=on
PINHD-2X9M .228 | D22-53 | 2 | 0.60 | 1.20 | Harwin | M20-9760942 | DigiKey | 952-1825-ND | http://www.digikey.com/product-search/en?WT.z_header=search_go&lang=en&site=us&x=11&y=12&formaction=on
Resistor 1 M | R1 | 1 | 0.03 | 0.03 | Stackpole Electronics | CF14JT1M00 | DigiKey | CF14JT1M00CT-ND | http://www.digikey.com/product-detail/en/CF14JT1M00/CF14JT1M00CT-ND/1830423
M25 SubD connector | X1 | 1 | 1.18 | 1.18 | FCI | 10090097-P254VLF | DigiKey | 609-4006-ND | http://www.digikey.com/product-search/en?WT.z_header=search_go&lang=en&site=us&x=11&y=16&formaction=on
DB-25 female | X2 | 1 | 1.18 | 1.18 | FCI | 10090099-S254VLF | DigiKey | 609-4012-ND | http://www.digikey.com/product-search/en?WT.z_header=search_go&lang=en&site=us&x=15&y=16&formaction=on
DB-15 -male | X3 | 1 | 1.08 | 1.08 | Sullins Connector | SDS107-PRW1-M15-SN23-11 | DigiKey | S9569-ND | http://www.digikey.com/product-search/en?WT.z_header=search_go&lang=en&site=us&x=18&y=17&formaction=on
DB-9-F | X4 | 1 | 0.64 | 0.64 | TE Connectivity | 1734348-1 | DigiKey | A35109-ND | http://www.digikey.com/product-search/en?WT.z_header=search_go&lang=en&site=us&x=12&y=12&formaction=on
DB-9-M | X5 | 1 | 0.83 | 0.83 | FCI | 10090097-P094VLF | DigiKey | 609-4003-ND | http://www.digikey.com/product-search/en?WT.z_header=search_go&lang=en&site=us&x=12&y=16&formaction=on
SHUNT | JP9:3-5,2-4 | 2 | 0.10 | 0.20 | TE Connectivity | 382811-8 | DigiKey | A26228-ND | http://www.digikey.com/product-search/en?WT.z_header=search_go&lang=en&site=us&x=16&y=15&formaction=on
PINHD-2X3M | ICSP,JP9 | 2 | 0.22 | 0.44 | Sullins Connector | PREC003DAAN-RC | DigiKey | S2012EC-03-ND | http://www.digikey.com/product-detail/en/PREC003DAAN-RC/S2012EC-03-ND/2774891
DAC MCP 4802 | IC2,IC3 | 2 | 1.48 | 2.96 | Microchip Tech | MCP4802-E/P | DigiKey | MCP4802-E/P-ND | http://www.digikey.com/product-search/en?WT.z_header=search_go&lang=en&site=us&x=11&y=13&formaction=on
0.1 uF Capacitor | C1,C2 | 2 | 0.10 | 0.20 | Kemet | C420C104K5R5TA7200 | DigiKey | 399-4491-1-ND | http://www.digikey.com/product-detail/en/C420C104K5R5TA7200/399-4491-1-ND/818348
Parts TOTAL |  |  |  | 46.87
Price |  |  |  | 90.00
Not used
PINHD-1X8M .32 | too long | 2 | 0.80 |  | Samtec | TSW-108-14-L-S | DigiKey | SAM1055-08-ND | http://www.digikey.com/product-search/en?WT.z_header=search_go&lang=en&site=us&x=15&y=15&formaction=on
push button (reset) | PCB error | 2 | 0.44 | 0.88 | CW Industries | GPBS-800N | DigiKey | CW178-ND | http://www.digikey.com/product-search/en?WT.z_header=search_go&lang=en&site=us&x=14&y=13&formaction=on
Socket-2X3F ICSP1 | Not needed | 1 | 0.88 |  | TE Connectivity | 215307-3 | DigiKey | A106656-ND | http://www.digikey.com/product-search/en?WT.z_header=search_go&lang=en&site=us&x=10&y=17&formaction=on
Enhanced version
Wire, 200mm | ANT1 | 1
Transistor, NPN C8050 | Q1,Q2 | 2 |  |  |  |  | DigiKey | 497-2586-5-ND
Flip-flop | IC1 | 1 |  |  |  |  | DigiKey | 497-1346-5-ND
4-Channel UHF Receiver | JP5, JP6 | 1 |  |  |  | H01749-01U | Hobby Engineering
Diode | D1 | 1 |  |  |  |  | DigiKey | 641-1311-1-ND
Res, 10 M | R2,R5,R6,R8 | 4 |  |  |  |  | DigiKey | CF14JT10M00CT-ND
Res, 1.5K | R3,R7 | 2 |  |  |  |  | DigiKey
Res, 1M | R4 | 1 |  |  |  |  | DigiKey | CF14JT1M00CT-ND
0.1 uF Capacitor | C3,C4,C5 | 3 |  |  |  |  | DigiKey | 399-4491-1-ND
Purchased separately
Arduino Mega 2560 |  | 1 | 55.13 | 55.13 | Arduino |  | Robot Shop | RB-Ard-33
Off-Board
4-Channel UHF Transmitter |  |  |  |  |  | H01747-01Y | Hobby Engineering
DB-25 pin though 2m, male-male cable |  |  |  |  |  |  | DigiKey | AE9867-ND
DB-25 pin though 2m, female-female cable
Relay |  | 1 | 4.02 |  | Panasonic | ALF1P12 | DigiKey | 255-2099-5-ND | http://www.digikey.com/product-search/en?WT.z_header=search_go&lang=en&site=us&x=11&y=17&formaction=on
C1 Circuit board and box for relay.
DB-15 -male for C1 box.
DB-25 female for C6 box.
Wiring from C1 box to joystick/controller.
Current sensor in C1 box.
Connectors in C2 from servo controllers to PCB.
DB-15 cable |  |  |  |  |  |  | DigiKey | H7SSH-1506G-ND
DB-9 cable |  |  |  |  |  |  | DigiKey | AE9880-ND

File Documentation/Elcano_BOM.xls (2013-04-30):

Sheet: Sheet1
Elcano Bill of Materials
Description | Price (US $) | Weight (lb) | Source | Comment
Mechanical subtotal | 2579 | 31.4
Aluminum rack | 15 | 0.5 | Hardware store | Build rack from 1/16”x1/2”x6' Aluminum angle.
Navigation subsystem | 563
3 project boxes | 30 | 3 | Fryes; Twin Industries part# b30-7100 | 6.3”x3.7”x2.4” with proto boards.
Colored Anderson housings and powerpole contacts | 40 |  | Powerwerx.com | These give a secure connection. Buy an Anderson crimping tool. Price is for about 200 connectors.
MegaShieldDB | 105 |  |  | Four remote operated relays. Used for stop / go and emergency stop.
Arduino Mega for C2 | 24 |  | http://lightake.com | Dual control unit selects from driver joystick or C1 cruise control.
One ACS758LCB-050U current sensors | 7 |  | Newark Electronics | Sense the power draw to the three actuators
APEM 9000 Joystick | 110 |  | DigiKey | Driver has no mechanical control of the vehicle. Joystick is not needed for Robomagellan.
joystick enclosure, connector, relay etc. | 25
Parts for brake & steer servo control | 30
Parts for front panel | 60
Cable DB25 M-M | 7 |  | DigiKey
Cable DB25 F-F | 7 |  | DigiKey
Cable DB15 F-F | 7 |  | DigiKey
Data logging shield for C2 | 20 |  | http://www.adafruit.com/category/17 | You can record everything on an SD card, then analyze it in a spreadsheet on your laptop.
Arduino Nano for C3 | 11.5 |  | Various sources | Pilot
Arduino Nano for C4 | 11.5 |  | Various sources | Path planner
SD shield for C4 | 20
Raspberry Pi for C7 | 40
Web Camera | 20
Cruise shield | 55
TOTAL: | 3732 | 34.9
This come to about $3700 in materials, plus a whole lot of work. On completion, you will have a 50 lb dual mode vehicle capable of carrying a person.

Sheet: Navigation
Costs for building an Elcano vehicle |  | Updated 4/15/13
Navigation Subsystem
Description | Price (US $) | Weight (lb) | Source | Comment
Arduino Mega for C6 | 24 |  | http://lightake.com | Navigation unit uses GPS, odometer, compass, INU and digital map.
Arduino GPS data logging shield for C6 | 20 |  | http://www.adafruit.com/category/17 | SD card to analyze localization from sensor fusion.
EM-406A GPS module | 60 |  | http://www.adafruit.com/category/17
Cylometer | 25 |  | Bike store | Cut into wires from the Hall Effect odometry pick- ups and route them to the C6 computer.
UM-6 LT Orientation sensor | 149 |  | Polulu # 1256
Optical mouse odometer | 35 |  | Had been available from DIYdrones | An optical mouse sensor with the right lens
Front left: XL-MaxSonar 1200 | 50 |  | Pololu #1652 | Obstacle detection on C6
Front: XL-MaxSonar 1220 | 50 |  | Pololu #1650
Front right: XL-MaxSonar 1200 | 50 |  | www.Pololu.com #1650
right: XL-MaxSonar 1200 | 50
Left: XL-MaxSonar 1200 | 50
Total | 563

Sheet: Mechanical
Mechanical Subsystem
Description | Price (US $) | Weight (lb) | Source | Comment
 |  |  |  | There are many ways to build the system on a less expensive vehicle.
 |  |  | http://www.pjrc.com/teensy/ | An RC car would be a good choice, in which case Teensy Arduinos are appropriate.
Catrike Dash | 1350 | 17 | http://www.catrike.com/catrike_dash.html | Design works with any vehicle big enough to carry electronics, sensors and actuators.
Kelly E-bike controller | 169 | 4.5 | http://kellycontroller.com/keb48201x24v-48v150a20kw-bike-brushless-controller-regen-p-59.html | KEB48201X,24V-48V,150A,2.0KW, E-bike Brushless Controller /Regen
Controller waterproof option | 38 | 0 | same
20” rear wheel with hub motor | 295 |  | http://www.goldenmotor.com | May be heavy
2” stroke linear servo | 130 | 2.4 | http://servocity.com/html/12v_linear_actuators.html | Brake servo and controller: 25 lb thrust. Writing a PWM signal applies brakes. Present version from Servo City does not include a controller, but price is $130.
4” stroke linear servo | 130 | 2.5 | same | Steering servo and controller: 25 lb thrust. Writing a PWM signal turns wheels.
Two actuator mounting brackets | 22 |  | same
Brake lever pulling two cables | 15 |  | Bike shop | Connect disk brakes on front wheels to the lever.
Custom brake mount hardware | 15 |  | Need to machine parts. | Make parts to mount brake servo. A slotted PVC tube pushed by the servo applies the brake. Make sure rider can manually operate brake lever in an emergency.
Custom steering mount hardware. | 15 |  | Need to machine parts. | Steering servo is attached to steering tie bar. Vehicle is Ackerman steered.
Subtotal | 2179 | 26.4
Lead acid battery: 3 cells of 12 V and 6.5 Amp Hours each | 110 | 15.4 |  | Put batteries in series for 36V power to hub motor. The lower 12 V (or a separate battery) is used to power the servos and electronics.
Lithium battery | 400 | 5 | BatterySpace.com
Lead acid total: | 2289 | 41.8
Lithium Total: | 2579 | 31.4

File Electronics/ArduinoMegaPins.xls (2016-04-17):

Eagle CAD produced file giving positions of pins on the Arduino Mega.
 |  |  |  |  |  |  | relative position
Part | Value | Description | Library | x position | y position | Rotation | 4200 | 2600
IC4 | ATMEGA8U2-MU | QFN32 | atmel | 720 | 1500 | R90
IC3 | ATMEGA2560-16AU | TQFP100 | atmel-2005 | 2000 | 1116 | R0
D1 | M7 | SMB | diode | 725 | 475 | R180
L | YELLOW | CHIP-LED0805 | led | 1100 | 1650 | R90
ON | GREEN | CHIP-LED0805 | led | 3000 | 1450 | R90
RX | YELLOW | CHIP-LED0805 | led | 1100 | 1350 | R90
TX | YELLOW | CHIP-LED0805 | led | 1100 | 1450 | R90
IC1 | MC33269ST-5.0T3 | SOT223 | linear | 340 | 700 | R90
IC2 | MC33269D-5.0 | DPACK | linear | 275 | 700 | R90
IC5 | LM358D | SO08 | linear | 720 | 850 | R270
POWER | POWER | 1X06 | pinhead | 1550 | 100 | R0 | 2650 | 2500
A0-7 | ADCL | 1X08 | pinhead | 2350 | 100 | R0 | 1850 | 2500
A8-15 | ADCH | 1X08 | pinhead | 3250 | 100 | R0 | 950 | 2500
JP3 | JP3 | 1X01 | pinhead | 3700 | 300 | R0 | 500 | 2300
JP4 | JP4 | 1X01 | pinhead | 3800 | 300 | R0 | 400 | 2300
RESET-EN | RESET-EN | SJ | jumper | 1100 | 600 | R0 | 3100 | 2000
D38-53 | XIOL | 2X08 | pinhead | 3750 | 750 | R90 | 450 | 1850
ICSP | ICSP | 2X03 | pinhead | 2555 | 1100 | R270 | 1645 | 1500
GROUND | GROUND | SJ | jumper | 425 | 1300 | MR180 | 3775 | 1300
D22-37 | XIOH | 2X08 | pinhead | 3750 | 1550 | R90 | 450 | 1050
UBOOT | UBOOT | SJ | jumper | 830 | 1610 | MR90 | 3370 | 990
ICSP1 | ICSP | 2X03 | pinhead | 720 | 1820 | R180 | 3480 | 780
D8-13 | PWMH | 1X08 | pinhead | 1290 | 2000 | R180 | 2910 | 600
D0-7 | PWML | 1X08 | pinhead | 2150 | 2000 | R180 | 2050 | 600
D14-21 | COMMUNICATION | 1X08 | pinhead | 3050 | 2000 | R180 | 1150 | 600
JP1 | JP1 | 1X01 | pinhead | 3700 | 2000 | R0 | 500 | 600
JP2 | JP2 | 1X01 | pinhead | 3800 | 2000 | R0 | 400 | 600
 |  |  | hole | 550 | 100 |  | 3650 | 2500
 |  |  | hole | 2600 | 300 |  | 1600 | 2300
 |  |  | hole | 3800 | 100 |  | 400 | 2500
 |  |  | hole | 600 | 2000 |  | 3600 | 600
 |  |  | hole | 2600 | 1400 |  | 1600 | 1200
 |  |  | hole | 3550 | 2000 |  | 650 | 600
X1 | DC21MMX | DC-21MM | powersupply | 210 | 330 | R90
C11 | 100n | C0603 | rcl | 850 | 1000 | R0
C8 | 100n | C0603 | rcl | 600 | 1000 | R0
F1 | 500mA | L1812 | rcl | 175 | 1000 | R180
PC1 | 47u | PANASONIC_D | rcl | 800 | 225 | R90
PC2 | 47u | PANASONIC_D | rcl | 1100 | 225 | R90
RN1 | 10K | CAT16 | resistor-dil | 3175 | 1450 | R270
RN2 | 22R | CAY16 | resistor-dil | 475 | 1500 | R90
RN3 | 1k | CAY16 | resistor-dil | 1100 | 1550 | R270
RN4 | 1k | CAY16 | resistor-dil | 1100 | 1225 | R90
RN5 | 10K | CAT16 | resistor-dil | 725 | 650 | R90
C1 | 22p | C0603-ROUND | SmartPrj | 1100 | 525 | R180
C10 | 1u | C0603-ROUND | SmartPrj | 475 | 1725 | R180
C12 | 100n | C0603-ROUND | SmartPrj | 850 | 700 | R180
C13 | 100n | C0603-ROUND | SmartPrj | 1100 | 850 | R0
C14 | 22p | C0603-ROUND | SmartPrj | 1575 | 450 | R90
C15 | 22p | C0603-ROUND | SmartPrj | 1575 | 700 | R270
C16 | 22p | C0603-ROUND | SmartPrj | 600 | 1075 | R180
C17 | 22p | C0603-ROUND | SmartPrj | 850 | 1075 | R0
C2 | 100n | C0603-ROUND | SmartPrj | 600 | 700 | R0
C3 | 100n | C0603-ROUND | SmartPrj | 1100 | 1750 | R0
C4 | 100n | C0603-ROUND | SmartPrj | 1520 | 280 | R0
C5 | 100n | C0603-ROUND | SmartPrj | 2320 | 1550 | R0
C6 | 100n | C0603-ROUND | SmartPrj | 1576.5748 | 1197.59843 | R180
C7 | 100n | C0603-ROUND | SmartPrj | 1100 | 700 | R0
C9 | 100n | C0603-ROUND | SmartPrj | 850 | 1325 | R0
R1 | 1M | R0603-ROUND | SmartPrj | 1575 | 575 | R90
R2 | 1M | R0603-ROUND | SmartPrj | 725 | 1075 | R0
R3 | 27R | R0603-ROUND | SmartPrj | 1650 | 575 | R270
R4 | 27R | R0603-ROUND | SmartPrj | 600 | 1325 | R180
U$2 | FIDUCIALMOUNT | FIDUCIA-MOUNT | SmartPrj | 2789 | 1503.62992 | R0
U$3 | FIDUCIALMOUNT | FIDUCIA-MOUNT | SmartPrj | 105 | 95 | R0
U$4 | FIDUCIALMOUNT | FIDUCIA-MOUNT | SmartPrj | 780 | 2000 | R0
U$5 | FIDUCIALMOUNT | FIDUCIA-MOUNT | SmartPrj | 2000 | 1116 | R0
X2 | X2 | PN61729 | SmartPrj | 150 | 1500 | R270
Y1 | 16MHz | RESONATOR | SmartPrj | 1450 | 575 | R270
Y2 | 16MHz | RESONATOR | SmartPrj | 720 | 1200 | R180
Q1 | 16MHz | QS | special | 720 | 1200 | R180
Q2 | 16MHz | QS | special | 1450 | 575 | R270
RESET | TS42 | TS42 | st-mod | 2920 | 1100 | R90
IC6 | LP2985-33DBVR | SOT23-DBV | texas | 1100 | 991 | R180
Z1 | PGB1010604 | CT/CN0603 | varistor | 475 | 1400 | R0
Z2 | PGB1010604 | CT/CN0603 | varistor | 475 | 1600 | R0
L1 | BLM21 | 805 | wuerth-elektronik | 325 | 1780 | R180
T2 | FDN340P | SOT-23 | zetex | 375 | 1000 | R270

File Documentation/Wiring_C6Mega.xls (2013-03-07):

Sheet: C6 Navigator
Src/Dest | Wire color @ C6 | End Color | Dir | Signal | Mega
C2:5 | Green | Blue | > | Throttle | A00
C2:7 | Green | Green | > | DiskBrake | A01
C2:6 | Yellow | Yellow | > | Steer | A02
 |  |  |  |  | A03
 |  |  |  |  | A04
 |  |  |  |  | A05
 |  |  |  |  | A06
 |  |  |  |  | A07
 |  |  |  |  | A08
C3:9 |  | Blue | > | Cruise Throttle | A09
C3:10 |  | Green | > | Cruise Brake | A10
C3:11 |  | Yellow | > | Cruise Steer | A11
 |  |  |  |  | A12
 |  |  |  |  | A13
 |  |  |  |  | A14
 |  |  |  |  | A15
Serial Monitor in |  |  | > | Rx0; serial in | D00 (Rx0, D0 PWM)
Serial Monitor out |  |  | < | Tx0; serial out | D01 (Tx0, D1 PWM)
 |  |  |  |  | D02 Int 0
 |  |  |  |  | D03 Int 1
GPS J-11 6 |  |  |  | GPS Power | D04
GPS J-11 5 |  |  |  | GPS green LED | D05 PWM)
GPS J-11 4 |  |  |  | GPS red LED | D06 PWM)
GPS J-11 3 |  |  |  | GPS_PPS | D07 PWM)
GPS J-11 2 |  |  |  | GPS MMC_CD
GPS J-11 1 |  |  |  | GPS_MMC_WP
C3:A0 | Red | Black |  | Speed | D08
C3:A1 | Yellow | Gray |  | Direction | D09
Shield:D10 |  |  |  | Chip Select | D10
Shield:D11 |  |  |  | MOSI | D11
Shield:D12 |  |  |  | MISO | D12
Shield:D13 |  |  |  | CLK | D13
GPS J-11 7, Rx | Red | Red | < | GPS control | D14 TX3
GPS J-11 8, Tx | Orange | Orange | > | Location | D15 Rx3
C4:0 | Yellow | Orange | < | Navigation Fix | D16 Tx2
C4:3 | Green | Green | < | C6 Data available | D17 Rx2
INU:Rx | Blue |  | < | INU control | D18 Int 2, Tx1
INU:Tx | Brown |  | > | Bearing | D19 Int 3, Rx1
 | Gray |  |  |  | D20 Int 4
Cylclometer | Black |  | > | Odometer click | D21 INT 5
 | Red |  |  |  | Vcc
C2:4;C3:12 | Orange |  | > | Move OK | D23
 | Yellow |  |  |  | D25
 | Green |  |  |  | D27
 | Blue |  |  |  | D29
 | Brown |  |  |  | D31
 | Gray |  |  |  | D33
 | Black |  |  |  | D35
optical odometer |  |  |  |  | D49 LED
optical odometer |  |  |  |  | D50 MISO
optical odometer |  |  |  |  | D51 MOSI
optical odometer |  |  |  |  | D52 SCK
optical odometer |  |  |  |  | D53 SS

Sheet: C7 Vision
Src/Dest | Wire color | Connector Color | Dir | Signal | Mega | Source pin
C4:9 |  |  | > | Expected horizontal | A00
C4:10 |  |  | > | Expected vertical | A01
C4:11 |  |  | > | Expected size | A02
 |  |  |  |  | A03
 |  |  |  |  | A04
 |  |  |  |  | A05
 |  |  |  |  | A06
 |  |  |  |  | A07
 |  |  |  |  | A08
 |  |  |  |  | A09
 |  |  |  |  | A10
 |  |  |  |  | A11
 |  |  |  |  | A12
 |  |  |  |  | A13
 |  |  |  |  | A14
 |  |  |  |  | A15
Web cam |  | USB | > | Camera | D00 (Rx0, D0 PWM)
Web cam |  | USB | < | Camera control | D01 (Tx0, D1 PWM)
 |  |  |  |  | D02 Int 0
 |  |  |  |  | D03 Int 1
C4:A0 |  |  | < | Horizontal | D04
C4:A1 |  |  | < | Vertical | D05 PWM)
C4:A2 |  |  | < | Size | D06 PWM)
C4:A3 |  |  | < | Coneness | D07 PWM)
 |  |  |  |  | D08
 |  |  |  |  | D09
 |  |  |  |  | D10
 |  |  |  |  | D11
 |  |  |  |  | D12
 |  |  |  |  | D13
 |  |  |  |  | D14 TX3
 |  |  |  |  | D15 Rx3
 |  |  |  |  | D16 Tx2
 |  |  |  |  | D17 Rx2
 |  |  |  |  | D18 Int 2
 |  |  |  |  | D19 Int 3
 |  |  |  |  | D20 Int 4
 |  |  |  |  | D21 INT 5
 |  |  |  |  | D22-D53
 |  |  |  |  | P0 Reset
 |  |  |  |  | P1 3V3
 |  |  |  |  | P2 5V
 |  |  |  |  | P3 Gnd
 |  |  |  |  | P4 Gnd
 |  |  |  |  | P5 Vin

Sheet: C4 Path
Src/Dest | Color @ Arduino | End Color | Dir | Signal | 2009 | Source pin
C6:16 | Orange | Yellow | > | Navigation fix | J1:1 (RxD, D0)
C3:0 | Red | Red | < | Path | J1:2 (TxD, D1)
C6:17 | Green | Green | > | C6 Data available | J1:3 (D2 INT0)
C3:2 | Yellow | Yellow | < | C4 Data available | J1:4 (D3 INT1, PWM)
 |  |  |  |  | J1:5 (D4)
 |  |  |  |  | J1:6 (D5 PWM)
 |  |  |  |  | J1:7 (D6 PWM)
 |  |  |  |  | J1:8 (D7)
 |  |  |  |  | J3:1 (D8)
C7:A0 |  |  | < | Expected horizontal | J3:2 (D9 PWM)
C7:A1 |  |  | < | Expected vertical | J3:3 (D10 PWM)
C7:A2 |  |  | < | Expected size | J3:4 (D11 PWM)
 |  |  |  |  | J3:5 (D12)
 |  |  |  |  | J3:6 (D13)
 |  |  |  |  | J3:7 (Ground)
 |  |  |  |  | J3:8 (AREF)
C7:4 |  |  | > | Horizontal | J2:1 (ADC0/D14)
C7:5 |  |  | > | Vertical | J2:2 (ADC1/D15)
C7:6 |  |  | > | Size | J2:3 (ADC2/D16)
C7:7 |  |  | > | Coneness | J2:4 (ADC3/D17)
L-3 |  |  | > | Sonar range | J2:5 (ADC4/D18)
R-3 |  |  | > | Sonar range | J2:6 (ADC5/D19)

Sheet: C3 Pilot
Src/Dest | Color @ Arduino | End color | Dir | Signal | 2009
C4:1 | Red | Red | > | Path | J1:1 (RxD, D0)
 |  |  |  |  | J1:2 (TxD, D1)
C4:3 | Yellow | Yellow | > | C4 Data available | J1:3 (D2 INT0)
 |  |  |  |  | J1:4 (D3 INT1, PWM)
 |  |  |  |  | J1:5 (D4)
F-1 |  |  | < | Chaining | J1:6 (D5 PWM)
Relay |  |  | < | Power FL,FR | J1:7 (D6 PWM)
Relay |  |  | < | Power F | J1:8 (D7)
 |  |  |  |  | J3:1 (D8)
C2:A9, C6:A9 |  |  | < | Cruise Throttle | J3:2 (D9 PWM)
C2:A10,C6:A10 |  |  | < | Cruise Brake | J3:3 (D10 PWM)
C2:A11,C6:A11 |  |  | < | Cruise Steer | J3:4 (D11 PWM)
C2:4;C6:23 |  |  | > | Move OK | J3:5 (D12)
 |  |  |  |  | J3:6 (D13)
 |  |  |  |  | J3:7 (Ground)
 |  |  |  |  | J3:8 (AREF)
C6:8 |  |  | > | Speed | J2:1 (A0)
C6:9 |  |  | > | Direction | J2:2 (A1)
 |  |  | > |  | J2:3 (A2)
F-3 | Green | Yellow | > | Sonar range | J2:4 (A3)
FL-3 | Green | Orange | > | Sonar range | J2:5 (A4)
FR-3 | Green | Red | > | Sonar range | J2:6 (A5)
 |  | (none) |  |  | P0 Reset
 |  | (none) |  |  | P1 3V3
F-1 | Orange | Black | < | Select Tx / chaining | P2 5V
F-4 | Blue | Black | < | Enable ranging | P2 5V
F-6 | Gray | Black | < | Vcc | P2 5V
FL-1 | Orange | Black | < | Select Tx / chaining | P2 5V
FL-4 | Blue | Black | < | Enable ranging | P2 5V
FL-6 | Gray | Black | < | Vcc | P2 5V
FR-1 | Orange | Black | < | Select Tx / chaining | P2 5V
FR-4 | Blue | Black | < | Enable ranging | P2 5V
FR-6 | Gray | Black | < | Vcc | P2 5V
F-7 | Black | Gray |  | Ground | P3 Gnd
FL-7 | Black | Gray |  | Ground | P3 Gnd
FR-7 | Black | Gray |  | Ground | P3 Gnd
(none) | (none) | Brown |  |  | P4 Gnd
(none) | (none) | Blue |  |  | P5 Vin
(none) | (none) | Green |  |  | P6 (none)
F-0 | Red | (none) |  | (none)
F-2 | Yellow | (none) | > | Pulse width
F-5 | Brown | (none) | > | Tx serial out
FL-0 | Red | (none) |  | (none)
FL-2 | Yellow | (none) | > | Pulse width
FL-5 | Brown | (none) | > | Tx serial out
FR-0 | Red | (none) |  | (none)
FR-2 | Yellow | (none) | > | Pulse width
FR-5 | Brown | (none) | > | Tx serial out

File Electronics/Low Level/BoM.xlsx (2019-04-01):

Qty | Device Name | Value | In BoM? | Digikey Part Number | Package | Part Label | Description | DESCRIPTION | DIGI-KEY_PART_NUMBER | DIGI-KEY_PURCHASE_URL | MANUFACTURER_PART_NUMBER | MF | MP | MPN | OC_FARNELL | OC_NEWARK | PACKAGE | PROD_ID | SF_SKU | SPICEPREFIX | VALUE | VENDOR
4 | 3mm green LED |  | yes | 732-5008-ND | LED3MM | 24V_ACTIVE, BRAKES_ON | LED
2 | C-USC1206 | 33pF | yes | 732-7873-1-ND (https://www.digikey.com/product-detail/en/wurth-electronics-inc/885012008020/732-7873-1-ND/5454500) | C1206 | C5, C6 | CAPACITOR, American symbol
2 | C-USC1206 | 560pF | yes | 311-4436-1-ND (https://www.digikey.com/product-detail/en/yageo/CC1206JRNPOBBN561/311-4436-1-ND/8025525) | C1206 | C7, C8 | CAPACITOR, American symbol
5 | C-USC1206 | 0.1uF | yes | 732-8086-1-ND (https://www.digikey.com/product-detail/en/wurth-electronics-inc/885012208009/732-8086-1-ND/5454713) | C1206 | C10, C11, C12, C13, C14 | CAPACITOR, American symbol
4 | C-USC1206 | 1uF | yes | 732-7685-1-ND (https://www.digikey.com/product-detail/en/wurth-electronics-inc/885012208013/732-7685-1-ND/5454312) | C1206 | C1, C2, C3, C4, C9, C15, C16 | CAPACITOR, American symbol
2 | R-US_R1206 | 100 | yes | 311-100FRCT-ND (https://www.digikey.com/product-detail/en/yageo/RC1206FR-07100RL/311-100FRCT-ND/731438) | R1206 | R7, R8 | RESISTOR, American symbol
4 | R-US_R1206 | 4.7K | yes | A106078CT-ND (https://www.digikey.com/product-detail/en/te-connectivity-passive-product/CRG1206F4K7/A106078CT-ND/3477735) | R1206 | R1, R2, R3, R4, R9, R17 | RESISTOR, American symbol
3 | R-US_R1206 | 10k | yes | RMCF1206JT10K0CT-ND (https://www.digikey.com/product-detail/en/stackpole-electronics-inc/RMCF1206JT10K0/RMCF1206JT10K0CT-ND/1942803) | R1206 | R12, R15, R16 | RESISTOR, American symbol
1 | R-US_R1206 | 120 | yes | A129547CT-ND (https://www.digikey.com/product-detail/en/te-connectivity-passive-product/CRGH1206F120R/A129547CT-ND/8566751) | R1206 | R10 | RESISTOR, American symbol
7 | R-US_R1206 | 1K | yes | RNCP1206FTD1K00CT-ND (https://www.digikey.com/product-detail/en/stackpole-electronics-inc/RNCP1206FTD1K00/RNCP1206FTD1K00CT-ND/2240675) | R1206 | R5, R6, R13, R18, R19 | RESISTOR, American symbol
1 | R-US_R1206 | 20K | yes | RNCP1206FTD20K0CT-ND (https://www.digikey.com/product-detail/en/stackpole-electronics-inc/RNCP1206FTD20K0/RNCP1206FTD20K0CT-ND/2240718) | R1206 | R14 | RESISTOR, American symbol
1 | 16MHz crystal | 16MHz | Yes | XC1759-ND | XTAL_ECS-160-20-46X | Q1 | QUARTZ CRYSTAL T/H | Crystal 16MHz ¬±30ppm _Tol_ ¬±50ppm _Stability_ 20pF FUND 50Ohm | XC1759-ND | https://www.digikey.com/product-detail/en/ecs-inc/ECS-160-20-46X/XC1759-ND/2676589 |  | ECS Inc. | ECS-160-20-46X |  |  |  | HC46/X ECS International |  |  | B
2 | 1N4148DO35-7 | 1N4148DO35-7 | yes | 1N4148FSCT-ND | DO35-7 | D2, D3 | DIODE
1 | 1N5400 | 1N5400 | yes | 1N5400-BDI-ND | DO201-15 | D1 | DIODE
1 | 284512-4 | 284512-4 | yes | A98398-ND | 284512-4 | X1 |  |  |  |  | 2845124 |  |  |  |  |  |  |  |  |  |  | TE Connectivity
2 | 2N3904 | 2N3904 | yes | 2N3904-APCT-ND | TO92 | T1, T2 | NPN TRANSISTOR
1 | BUZZER-PTH | BUZZER-PTH | Yes | 102-1153-ND | BUZZER-12MM | LS1 | Buzzer |  |  |  |  |  |  |  |  |  |  | COMP-08253 | COM-07950
2 | ORWH-SH-105D1F,000 | ORWH-SH-105D1F,000 | Yes | PB2032-ND | TE_ORWH-SH-105D1F,000 | PB1_BRAKE_ON, PB2_12/24 | General Purpose Relay, ORWH Series, Power, Non Latching, SPDT, 5 VDC, 10 A | General Purpose Relay, ORWH Series, Power, Non Latching, SPDT, 5 VDC, 10 A | PB2032-ND | https://www.digikey.com/product-detail/en/te-connectivity-potter-brumfield-relays/ORWH-SH-105D1F,000/PB2032-ND/4925028 |  | TE | ORWH-SH-105D1F,000 |  |  |  | None
1 | PESD1CAN | PESD1CAN | Yes | 1727-3817-1-ND | SPARKFUN-DISCRETESEMI_SOT23-3 | D4 | CAN bus ESD protection diode |  |  |  |  |  |  |  |  |  |  |  |  | J
1 | MCP2515(MCP2510)P | MCP2515 | yes | MCP2515-I/P-ND | DIP18 | IC1_2515 | CAN controller with SPI interface |  |  |  |  |  |  |  |  |  |  | NA-XXXXX |  | X | MCP2515
1 | MCP2551DIL08 | MCP2551DIL08 | Yes | MCP2551-E/P-ND‎ | IC-PACKAGE_DIL08 | IC2_2551 | CAN transceiver |  |  |  |  |  |  |  |  |  |  |  |  | X
1 | DIL8 | MCP4802 | Yes | MCP4802-E/P-ND | DIL08 | IC3_4802 | Dual In Line / Socket
1 | MOMENTARY-SWITCH-SPST-PTH-6.0MM | MOMENTARY-SWITCH-SPST-PTH-6.0MM | Yes | 450-1650-ND‎ | TACTILE_SWITCH_PTH_6.0MM | RESET | Momentary Switch (Pushbutton) - SPST |  |  |  |  |  |  |  |  |  |  | SWCH-08441 | COM-00097
1 | CONN_03-SCREW-5MM |  | yes | 732-2031-ND (https://www.digikey.com/product-detail/en/wurth-electronics-inc/691111710003/732-2031-ND/2060527) | SCREWTERMINAL-5MM-3 | CAN_HEADER | Multi connection point. Often used as Generic Header-pin footprint for 0.1 inch spaced/style header connections |  |  |  |  |  |  |  |  |  |  | CONN-10134 | PRT-08433
1 | RJ45 8 pin jack | RJ45-8L-B |  |  |  | Steering Header | Modular jack for steering peripherals
1 | DB9FEMALE | DB9 Plug | Yes | 182-09ME-ND‎ | DB9 | CANBUS | DB9 Connector |  |  |  |  |  |  |  |  |  |  | CONN-08194 |  | X
1 | M15-182 | DB-15 | Yes | AE10976-ND | 182-015-MALE | X3 | SUB-D |  |  |  |  |  |  |  | unknown | unknown
1 | ODO_JACK | CLICK | Yes | ‎MJ1-2503A‎ | ODO_JACK | X4
1 | PINHD-1X2 |  |  |  | 1X02 | E-STOP | PIN HEADER
1 | PINHD-1X6 |  |  |  | 1X06 | POWER | PIN HEADER
1 | PINHD-2X3 | ICSP |  |  | 2X03 | ICSP | PIN HEADER
1 | PINHD-1X8 | Digital 0-7 |  |  | 1X08 | DIGITAL_0-7 | PIN HEADER
1 | PINHD-1X8 | Digital 14-21 |  |  | 1X08 | DIGITAL_14-21 | PIN HEADER
1 | PINHD-1X8 | Analog In 0-7 |  |  | 1X08 | ADCL | PIN HEADER
1 | PINHD-1X8 | Analog In 8-15 |  |  | 1X08 | ADCH | PIN HEADER
1 | PINHEAD_PINHD-2X18 | Digital 22-53 |  |  | PINHEAD_2X18 | MEGA_EXPANSION | PIN HEADER
1 | PINHD-1X10 | Digital 8-13 |  |  | 1X10 | DIGITAL_8-13 | PIN HEADER

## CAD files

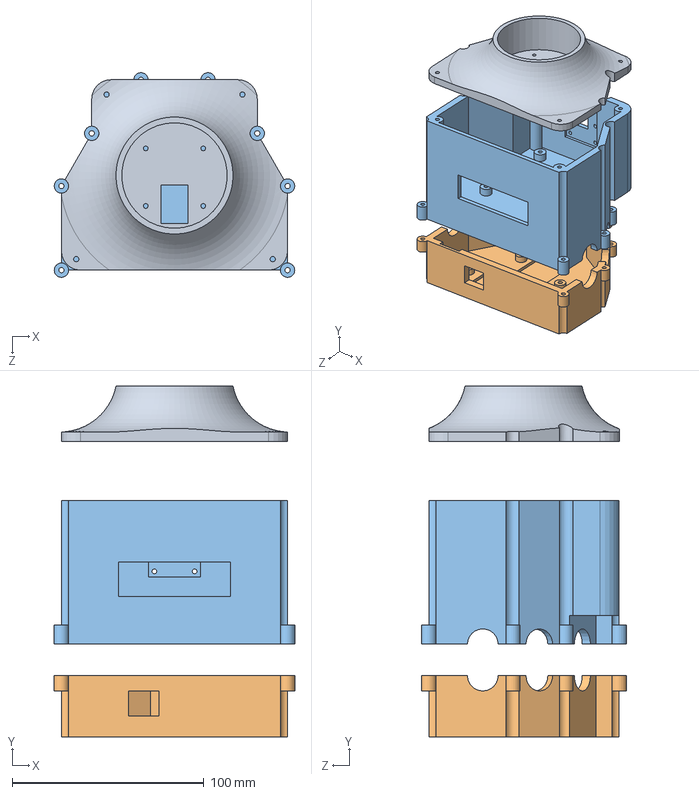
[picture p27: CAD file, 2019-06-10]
Mechanical/ELF/LIDAR/Main.SLDASM
125.5 x 183.1 x 106.8 mm
Lidar Top
Sonar Base
Sonar Top

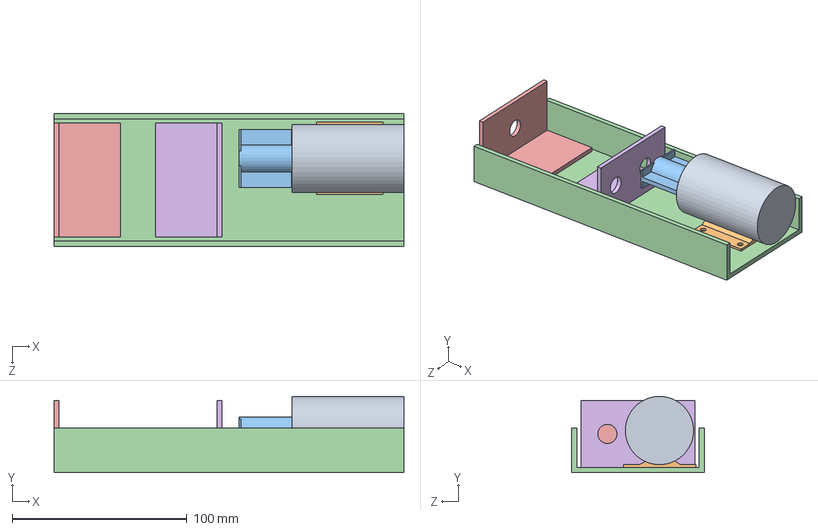
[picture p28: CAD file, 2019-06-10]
Mechanical/ELF/Brake_System/Brake_System/Assem1.SLDASM
200.0 x 43.5 x 76.2 mm
Solenoid Body
Solenoid Plate
Solenoid Rod
Solenoid Housing
Solenoid Front 90'
Solenoid Back 90'

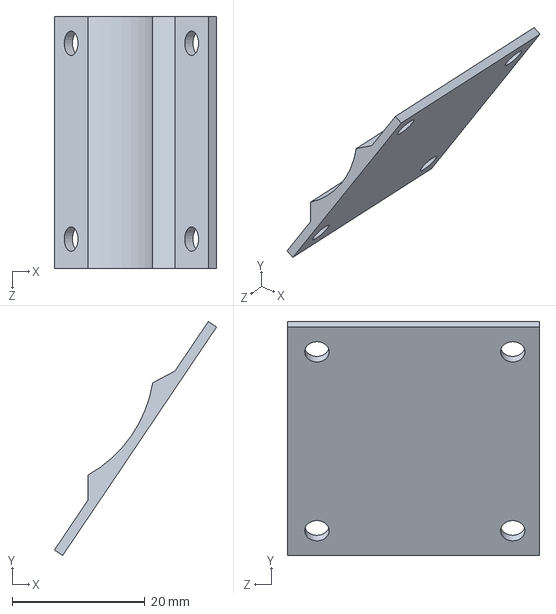
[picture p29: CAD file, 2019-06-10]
Mechanical/ELF/Brake_System/Brake_System/Solenoid Plate.SLDPRT
24.4 x 35.3 x 38.0 mm

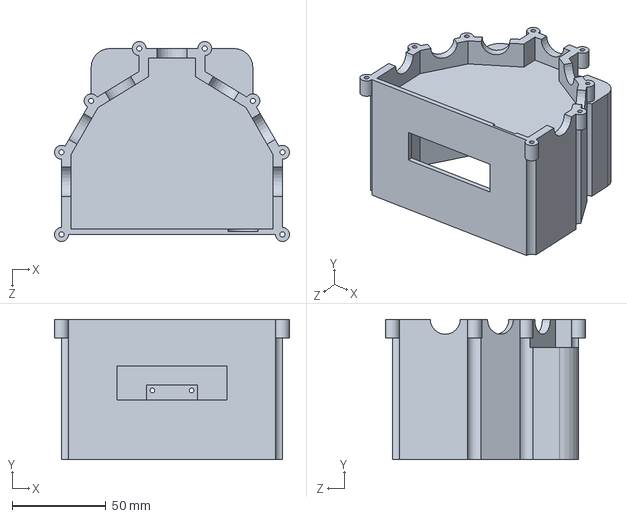
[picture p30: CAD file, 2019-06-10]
Mechanical/ELF/LIDAR/Sonar Top.SLDPRT
125.5 x 75.0 x 106.8 mm

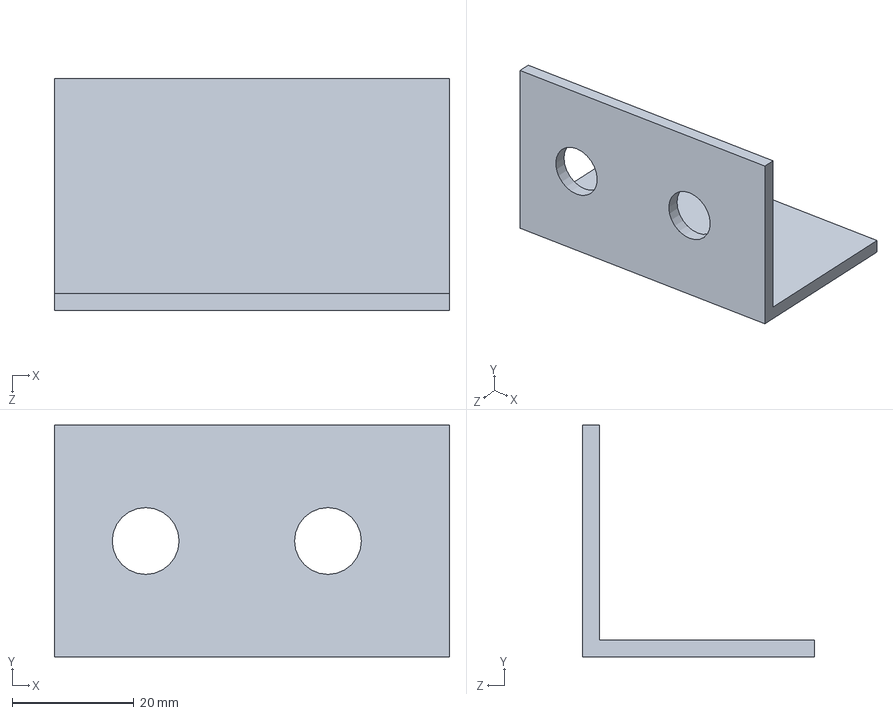
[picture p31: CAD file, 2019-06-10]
Mechanical/ELF/Brake_System/Brake_System/Solenoid Back 90'.SLDPRT
65.0 x 38.1 x 38.1 mm

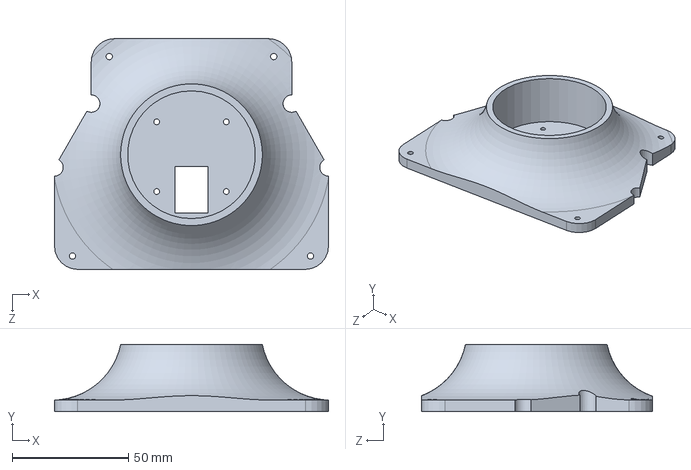
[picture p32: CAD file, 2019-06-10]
Mechanical/ELF/LIDAR/Lidar Top.SLDPRT
118.0 x 29.0 x 99.4 mm

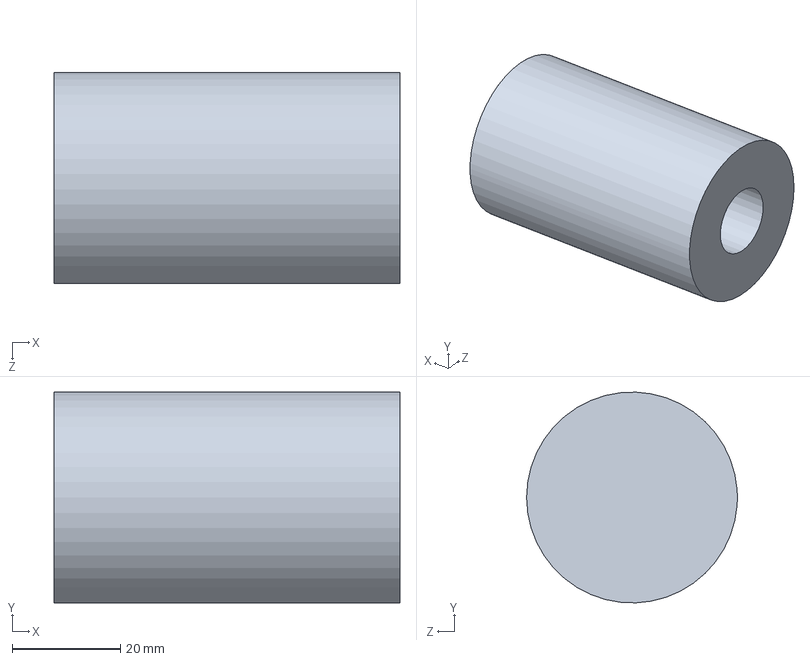
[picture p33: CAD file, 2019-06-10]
Mechanical/ELF/Brake_System/Brake_System/Solenoid Body.SLDPRT
64.0 x 39.0 x 39.0 mm

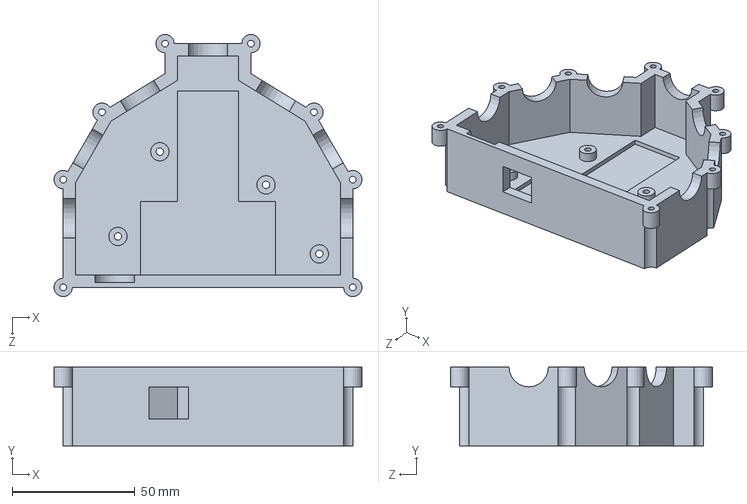
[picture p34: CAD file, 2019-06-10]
Mechanical/ELF/LIDAR/Sonar Base.SLDPRT
125.5 x 32.0 x 106.8 mm

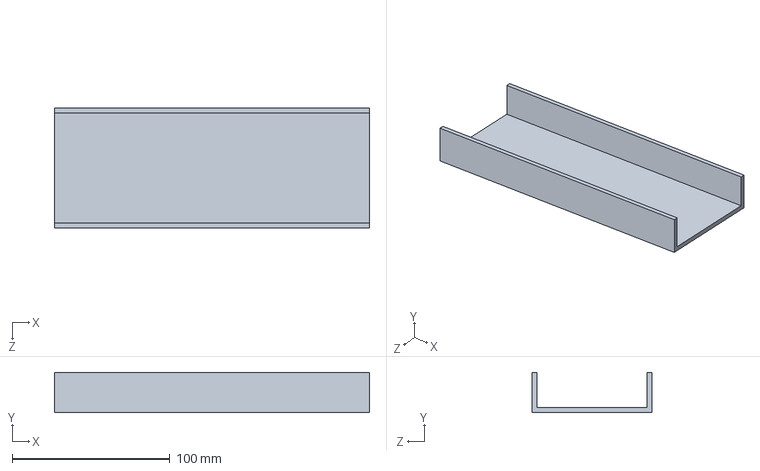
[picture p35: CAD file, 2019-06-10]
Mechanical/ELF/Brake_System/Brake_System/Solenoid Housing.SLDPRT
200.0 x 25.4 x 76.2 mm

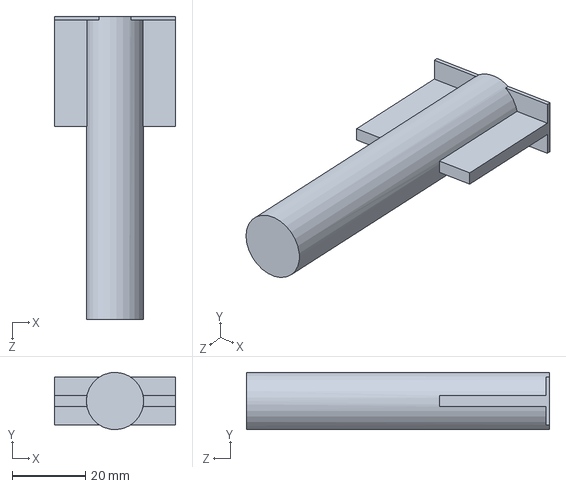
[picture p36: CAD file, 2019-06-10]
Mechanical/ELF/Brake_System/Brake_System/Solenoid Rod.SLDPRT
33.0 x 15.6 x 82.5 mm

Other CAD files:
hardware/Actuator Cap.sldprt
Mechanical/ELF/Brake_System/Brake_System/Solenoid Front 90'.SLDPRT
hardware/Actuator Cap.stl

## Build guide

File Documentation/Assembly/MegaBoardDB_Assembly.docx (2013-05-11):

# MegaBoardDB

Assembly Instructions

Take Photos of every step and add to this document.

# Parts list:

- MegaBoardDB Arduino shield (Qty: 1)
- 8-pin long tailed sockets - (Qty: 3)
- 6-pin long tailed socket - (Qty: 1)
- 8-pin headers - (Qty: 2)
- 2x18 pin header - (Qty: 1)
- 8-pin DIP integrated circuits - (Qty: 2)
- 0.1 uF Capacitors - (Qty: 2)
- 6 pin In-Circuit Serial Programming (ICSP) Sockets - (Qty: 1)
- DB25-Male connector - (Qty: 1)
- DB25-Female connector - (Qty: 1)
- DB15-Male connector - (Qty: 1)
- DB9-Female connector - (Qty: 1)
- DB9-Male connector - (Qty: 1)
- 2x6 pin header (Qty: 2)
- 1M Ω (Brown Black Green) resistor - (Qty: 1)
- Jumper - (Qty: 1)

# Assembly instruction:

## Without Wireless E-Stop:

1 ADCL, POWER, PWML, and PWMH shield stacking headers for Arduino
  a Find:
    - 8-pin long tailed sockets (Qty: 3) for PWML (D0-7), PWMH (D8-13), and ADCL (A0-7)
    - 6-pin long tailed socket (Qty: 1) for POWER
  b The analog-in socket is 8-pins, even though there are only 6-pins on shields.
  c Place MegaShieldDB board on up position (Text visible)
  d Secure sockets in a shield
  e Flip the board down.
  f Solder all 30 pins in place, making sure to maintain proper alignment with the Arduino board.
2 ADCH, COMMUNICATION, XIOL, and XIOH headers
  a Get:
    - 8-pin headers (Qty: 2) for ADCH (A8-15) and COMMUNICATION (D14-21)
    - 2x18 pin header (Qty: 1) for XIOL and XIOH (DIGITAL)
  b Place the long tails of the three connectors into sockets on an Arduino Mega board.
  c Place MegaShieldDB board on up position on top of the MegaShieldDB.
  d Align the Arduino Mega and the MegaShieldDB, so that the short pins on the three new headers stick though the board. (There will be a gap on the long-tailed sockets from step 1.)
  e Solder all 52 connector pins.
3 Integrated Circuits (IC)
  a 8-pin DIP integrated circuits:
    - IC2 - on the right with notch down (closer to IC2 text).
    - IC3 - on the left with notch up (closer to IC3 text).
  b With the MegaShieldDB board on up position, place these two IC.
  c Flip the board down.
  d Solder these IC in place.
4 Capacitors
  a Place two capacitors (0.1 uF):
    - C1 and C2 next to the ICs you just added.
  b They are ceramic and it doesn't matter which end is which.
  c Solder these in place.
  d Flip the MegaShield Snip off the leads after soldering.
5 In-Circuit Serial Programming (ICSP) Sockets
  a Place the 6-pin ICSP socket on the Arduino ICSP pins
  b Line up Arduino and MegaBoardDB.
  c Solder the ICSP connector into MegaBoardDB.
6 DB connectors
  a Snaps DB connectors into the board:
    - X1 - DB25-Male connector
    - X2 - DB25-Female connector
    - X3 - DB15-Male connector
    - X4 - DB9-Female connector
    - X5 - DB9-Male connector
  b Solder DB connectors in place
7 ICSP and JP9
  a Find:
    - 2x6 pin header (Qty: 2)
  c Place and Solder ICSP and JP9
8 Resistor
  a Place and Solder R1 (1M Ω - Brown Black Green)
9 Jumper setting
  a For without wireless E-Stop setting, place jumper on the JP9 (pin 3 and 5)

# Wireless E-Stop

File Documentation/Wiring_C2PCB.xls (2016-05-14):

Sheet: Internal
Current as of 4/16/16 |  |  | We no longer use the power distribution posts or the current sensors
 |  |  | Some other signals are no longer used.
Src | Dest | Connector | Dir | Signal | Mega | Notes
3 | 3 | (DAC) |  | Select CD | D49 | Select IC 3 DAC (channels C and D)
3 | 3 | (DAC) |  | (SS) Select AB | D53 | Select IC 2 DAC (channels A and B)
3 | 3 | (Rcvr 10) | > | Stop RC-2 | D18 Int 2 | A remote stop button generates an interrupt to stop the vehicle.
3 | 3 | (Rcvr 11) | > | Cruise RC-1 | D19 Int 3 | A remote cruise button starts enabled cruise systems.
3 | 1 | Black Anderson | - | Ground |  | Ground
3 | 3 | ICSP-1 |  | (MISO) | D50
 | 3 | ICSP-2 |  | 5V | 5V
 | 3 | ICSP-3 |  | (SCK) | D52
 | 3 | ICSP-4 |  | (MOSI) | D51
3 | 3 | ICSP-5 |  | Reset | Reset
3 | 3 | ICSP-6 |  | Ground | GND | Ground
3 | 1 | orange Anderson | > | 12 v power |  | Power goes to servo controllers, which produce the 5V to drive Arduino.
3 | 10 | Shield |  | Chip Select | D10 | Signals D10-13 are not brought out on connectors, and may be used by a shield.
3 | 10 | Shield |  | MOSI | D11 | “
3 | 10 | Shield |  | MISO | D12 | “
3 | 10 | Shield |  | CLK | D13 | “
3 | 0 | USB_Rx | > | Rx0; serial in | D00 (Rx0, D0 PWM) | Rx0 and Tx0 may be used by the monitor.
3 | 0 | USB_Tx | < | Tx0; serial out | D01 (Tx0, D1 PWM) | “
3 | 1 | X1-01 | < | LED 6 out | D33 | The LED outputs may display status information on the panel.
3 | 1 | X1-02 | < | LED 5 out | D31
3 | 1 | X1-03 | < | LED 4 out | D29
3 | 1 | X1-04 | < | LED 3 out | D27
3 | 1 | X1-05 | < | LED 1 out | D23
3 | 1 | X1-06 | > | EnableSteer | D22 | Panel switch: Whether steering can be autonomous.
3 | 1 | X1-07 | > | EnableBrake | D24 | Whether brakes can be autonomous.
3 | 1 | X1-08 | > | EnableThrottle | D26 | Whether the throttle can be autonomous.
3 | 1 | X1-09 | < | Cruise LED | D28 | Panel LED lights when under autonomous control.
3 | 1 | X1-10 | < | Stop LED | D30 | Panel LED lights when vehicle stop is commanded.
3 | 1 | X1-11 | < | Reverse LED | D32 | Vehicle is in reverse (not implemented)
3 | 1 | X1-12 | > | Reverse button | D34 | Button requesting reverse (not implemented)
3 | 1 | X1-13 | > | Cruise reverse | D36 | Autonomous request for reverse (not implemented)
9 | 1 | X1-14 | < | 36 V fuel | X3-8 | This is a 36V signal line that gives the state of the battery charge; used to drive LEDs.
3 | 1 | X1-15 | < | LED 7 out | D35
3 | 1 | X1-16 | < | LED 8 out | D37
3 | 1 | X1-17 | > | Cruise Button | D21 INT 5 | Panel cruise button starts enabled cruise systems
3 | 1 | X1-18 | > | Stop Button | D20 Int 4 | Panel stop button generates an interrupt to stop the vehicle.
3 | 1 | X1-19 |  | Available | D46 | Available for any digital input or output.
3 | 1 | X1-20 |  | Available | D44
3 | 1 | X1-21 |  | Available | D42
3 | 1 | X1-22 |  | Available | D40
3 | 1 | X1-23 |  | Available | D38
3 | 1 | X1-24 | > | 5 V from Steer | VCC | Main 5V supply. May be source or output.
3 | 1 | X1-25 | - | Ground | GND | Ground
3 | 6 | X2-01 | > | LED 6 in | X1-01 | Input for panel LEDs may come from off-board.
3 | 6 | X2-02 | > | LED 5 in | X1-02
3 | 6 | X2-03 | > | LED 4 in | X1-03
3 | 6 | X2-04 | > | LED 3 in | X1-04
3 | 6 | X2-05 | > | LED 1 in | X1-05
3 | 6 | X2-06 | > | Cruise Steer | A13 | Position of steering commanded by AI
3 | 6 | X2-07 | > | Cruise Brake | A14 | Position of brake commanded by AI
3 | 6 | X2-08 | > | Cruise Throttle | A15 | Position of throttle commanded by AI
3 | 6 | X2-09 | > | Speed Limit | A08 | Desired speed on this segment (not implemented).
3 | 6 | X2-10 | > | Speed | A12 | Actual speed (not implemented).
3 | 6 | X2-11 |  | Available | D41
3 | 6 | X2-12 |  | Available | D39
3 | 6 | X2-13 | > | Cruise Reverse | D36 | Reverse is commanded by AI (not implemented).
3 | 6 | X2-14 | < | Extra wireless | WLX / D0 | Jumper determines if this pin goes to D0 or unassigned wireless button.
3 | 6 | X2-15 | > | LED 7 in | X1-14
3 | 6 | X2-16 | > | LED 8 in | X1-15
3 | 6 | X2-17 | < | Move OK | D04 | Acknowledgement of receiving and executing move command (not implemented).
3 | 6 | X2-18 | > | Cruise Drive Cmd | D15 Rx3 | Message in Gamebots format giving wheel spin rate and steering angle.
3 | 6 | X2-19 |  | C2 Status | D14 TX3 | Feedback signal to AI with actual motion.
3 | 6 | X2-20 |  | Video in | D17 Rx2
3 | 6 | X2-21 | > | Wheel Rotation | D03 Int 1 | Reed switch generates one pulse per rotation.
3 | 6 | X2-22 |  | Video out | D16 Tx2
3 | 6 | X2-23 | > | Available | A06
7 | 6 | X2-24 | > | Secondary 5 V from Brake | X5-6 | May be used as power supply for AI.
3 | 6 | X2-25 | - | Ground | GND | Ground
1 | 9 | X3-01 | > | 36 V fuel | X1-25 | A 36V analog signal indicating battery charge; used to drive LEDs.
3 | 5 | X3-02 | > | SteerJoystick | A10 | Joystick left-right motion is for turning.
3 | 5 | X3-03 | > | JoystickCenter | A09 | This should be about 2.5V (128 counts) and is the joystick center. It is not important, since software uses a deadband.
3 | 9 | X3-04 | < | Reverse | D25 | REV_SW: Whether throttle drives trike forward (Low) or reverse (High)
3 | 9 | X3-05 |  | Regen brake | D43 | BRK_SW: Regenerative braking on/off
3 | 9 | X3-06 | < | Wireless Estop | D47/WLES | Remote request to turn off 36V power and stop the vehicle.
3 | 9 | X3-07 | > | Motor current | A00 | Indicates how much 36V current is being drawn.
3 | 5 | X3-08 | > | MotionJoystick | A11 | Joystick up motion is throttle; down motion is brake.
3 | 5 | X3-09 | > | Reverse button | D34 | Not implemented.
3 | 9 | X3-10 | > | ~Estop | D48 | This is the 5V supply produced by the E-bike controller. If it goes away, 36V power has been turned off (presumably by the rider's key switch).
3 | 9 | X3-11 | - | Ground | GND | Ground
3 | 9 | X3-12 | < | Analog Throttle | DACA | Motor throttle from the DAC.
3 | 9 | X3-13 | < | Analog Brake | DACB | BRK_AN: Amount of regenerative braking from the DAC
3 | 9 | X3-14 | > | Motor feedback | D02 Int 0 | A Hall signal from hub whose width is proportional to speed.
3 | 9 | X3-15 | < | WDPet | D05 PWM) | Stroke the watchdog. If pulse does not come in 250 ms, electronics applies e-stop
3 | 8 | X4-1 | - | Ground | GND | Ground
3 | 8 | X4-2 |  | Available | D08
3 | 8 | X4-3 | < | Analog C | DACC | A spare analog output from the DAC.
3 | 8 | X4-4 |  | Available | D45
3 | 8 | X4-5 | > | Available | A07
3 | 8 | X4-6 | > | Steer current | A04 | Current sensor (not implemented)
3 | 8 | X4-7 | > | Steer Feedback | A05 | Blue wire from servo gives servo position.
3 | 8 | X4-8 | > | 5 V from Steer | 5V | Servo produces 5V, used by MegaShieldDB
3 | 8 | X4-9 | < | Steer | D06 | PWM signal to turn vehicle
3 | 7 | X5-1 | - | Ground | GND | Ground
3 | 7 | X5-2 |  | Alternate Steer | D09 | Steer on #2
3 | 7 | X5-3 | < | Alternate Analog Throttle | DACD | Motor control on #2
3 | 7 | X5-4 |  | Ebrake | D47 | Remote request to e-stop the vehicle.
3 | 7 | X5-5 | > | Available | A03
3 | 7 | X5-6 | > | Brake Current | A02 | Current sensor (not implemented)
3 | 7 | X5-7 | > | Brake Feedback | A01 | Blue wire from servo gives servo position.
6 | 7 | X5-8 | > | Secondary 5 V from Brake | 5V | Servo produces 5V, routed to X2-24
3 | 7 | X5-9 | < | DiskBrake | D07 | PWM signal to apply brake
 |  |  |  | RC channel | D02 Int 0
 |  |  |  | RC channel | D18 Int 2
 |  |  |  | RC channel | D19 Int 3
 |  |  |  | RC channel | D20 Int 4
 |  |  |  | RC channel | D21 INT 5
 | 0 |  |  | Unspecified
 | 1 |  |  | Panel
 | 3 |  |  | Arduino
 | 5 |  |  | Joystick
 | 6 |  |  | Higher level computers
 | 7 |  |  | Brake controller
 | 8 |  |  | Steer controller
 | 9 |  |  | Motor controller
 | 10 |  |  | Shield
 | 12 |  |  | Battery

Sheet: Power
End 1 | Connector 1 | Wire color | Connector 2 | Signal | End 2
758 A signal | Molex | White-blue | Molex | Motor current | A00
758 B signal | Molex | Green-white | Molex | Steer current | A01
758 C signal | Molex | White-orange | Molex | Brake current | A02
Relay ground | Screw ground | Black thin | Soldered | Brake ground | Brake servo ground
To D07 | Green | Yellow | Soldered | Brake PWM signal | Brake servo signal
Battery ground | Black | Black | Ring | Fuse ground | Fuse ground post
Brake ground | Black | Black | Spade | Fuse 5A Brake | Fuse tab brake
Motor control ground | Black | Black | Spade | Fuse 2A Motor | Fuse tab motor
Battery 12 V | Orange | Black | Soldered | 12 V | Panel: power switch
Panel: Power switch acc | tab | White | Ring | Switched 12 V | Panel: Post 12 V
C1 and C3 5V | Pink |  | Ring | Brake 5V | Panel: Post 5 V
Joystick 5V | Pink | Red | Ring | Brake 5V | Panel: Post 5 V
C1 and C3 ground | Black | Black | Ring | Brake ground | Panel: Post ground
Joystick ground | Black | Black | Ring | Brake ground | Panel: Post ground
758 power | Soldered |  | Ring | Brake 5V | Post 1
Brake servo 5V | Soldered | Red thin | Ring | Brake 5V | Post 1
Panel: Post 5 V | Ring | Red | Ring | Brake 5V | Post 1
Relay: 1B, 2B | Soldered | 2 red thin | Ring | Brake 5V | Post 1
758 ground | Soldered | Black | Ring | Brake ground | Post 10
Brake servo ground | Soldered | Black thin | Ring | Brake ground | Post 10
Panel: Post ground | Ring | Black | Ring | Brake ground | Post 10
Fuse 5A steer | Soldered | Black | Ring | Steer ground | Post 2
Steer servo ground | Soldered | Black thin | Ring | Steer ground | Post 2
Battery 36 V | Red | Black | Ring | 36 V | Post 3
Relay: 4B | Screw 4B | Black | Ring | 36 V | Post 3
Relay 4C | Screw 4C | Black | Ring | Relay 36 V | Post 4
758 A out | Soldered | Black | Ring | Motor control 36 V | Post 4
758 A in | Soldered | Black | Ring | Relay 36 V | Post 5
Motor control 36 V | Red | Black | Ring | Motor control 36 V | Post 5
Steer servo 12 V | Soldered | Red thick | Ring | Steer 12 V | Post 6
758 C in | Soldered | Red | Ring | Switched 12 V | Post 6
758 C out | Soldered | Red | Ring | Steer 12 V | Post 8
Panel: Post 12 V | Ring | Green | Ring | Switched 12 V | Post 8
758 B out | Soldered | Red | Ring | Brake 12 V | Post 8
758 B in | Soldered | Red | Ring | Switched 12 V | Post 9
Brake servo 12 V | Soldered | Red thick | Ring | Brake 12 V | Post 9
Relay power | Screw 12 V | Green | Ring | Brake 12 V | Post 9
To D02 | Gray | Green | Screw 1C | Cruise RC-1 | Relay 1C
To D03 | White | White | Screw 2C | Stop RC-2 | Relay 2C
C4 … C8 5V | Pink | Red thin | Soldered | Steer 5V | Steer servo 5 V
C4 … C8 ground | Black | Black thin | Soldered | Steer ground | Steer servo ground
To D06 | Yellow | Yellow | Soldered | Steer PWM signal | Steer servo signal

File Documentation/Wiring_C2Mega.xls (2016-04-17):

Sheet: Internal
DEPRICATED |  |  | We no longer use the power distribution posts or the current sensors
Src/Dest | Src | Dest | Wire color | Connector Color | Dir | Signal | Mega | Formerly | Ex wire
Lower box ACS758 A | 3 | 2 | Green |  | > | 36V current | A00 | (Arduino duemillenove)
Lower box ACS758 B | 3 | 2 | Red |  | > | Steer current | A01
Lower box ACS758 C | 3 | 2 | Black |  | > | Brake Current | A02
reserved | 3 | 0 | White |  | > |  | A03
Shield | 3 | 10 |  |  | > | RTC SDA | A04
Shield | 3 | 10 |  |  | > | RTC SCL | A05
reserved | 3 | 0 |  |  | > |  | A06
reserved | 3 | 0 |  |  | > |  | A07
Brake servo blue | 3 | 7 | 4-Green | Blue | > | Brake Feedback | A08
Joystick Green | 3 | 5 | 4-Red | Green | > | JoystickCenter | A09 | A02 | Green
Joystick yellow | 3 | 5 | 4-Black | Yellow | > | SteerJoystick | A10 | A01 | Yellow
Joystick blue | 3 | 5 | 4-White | Blue | > | MotionJoystick | A11 | A00 | Blue
Steer servo blue | 3 | 8 | 3-Green | Blue (Purple) | > | Steer Feedback | A12
C3:9 | 3 | 6 | 3-Red | Yellow | > | Cruise Steer | A13 | A05 | Purple-black
C3:10 | 3 | 6 | 3-Black | Green | > | Cruise Brake | A14 | A04 | Blue
C3:11 | 3 | 6 | 3-White | Blue | > | Cruise Throttle | A15 | A03 | Tan-black
Serial Monitor in | 3 | 0 |  |  | > | Rx0; serial in | D00 (Rx0, D0 PWM)
Serial Monitor out | 3 | 0 |  |  | < | Tx0; serial out | D01 (Tx0, D1 PWM) |  | Red-black
Motor controller 5V | 3 | 9 | 1-Red |  | > | ~Estop | D02 Int 0 | D02 (NOR)
reserved | 3 | 0 |  |  |  |  | D03 Int 1
C3:12 | 3 | 6 |  |  | < | Move OK | D04
Motor controller,C3:A3,C6:A3 | 3 | 11 | Green | Blue | < | Traction motor Throttle | D05 PWM) | D09 | Green
Analog motor control | 11 | 9
Steer servo,C3:A4,C6:A4 | 3 | 8 | Yellow | Yellow | < | Steer | D06 PWM) | D10
Brake servo,C3:A5,C6:A5 | 3 | 7 | Green | Green | < | DiskBrake | D07 PWM) | D11
reserved | 3 | 0 |  |  |  |  | D08
reserved | 3 | 0 |  |  |  |  | D09
Shield | 3 | 10 |  |  |  | Chip Select | D10
Shield | 3 | 10 |  |  |  | MOSI | D11
Shield | 3 | 10 |  |  |  | MISO | D12
Shield | 3 | 10 |  |  |  | CLK | D13
reserved | 3 | 0 |  |  |  |  | D14 TX3
C3 Drive command | 3 | 6 |  |  | > | (serial) | D15 Rx3
reserved | 3 | 0 |  |  |  |  | D16 Tx2
reserved | 3 | 0 |  |  |  |  | D17 Rx2
Lower box: relay 2C | 3 | 4 |  |  | > | Stop RC-2 | D18 Int 2 | D02 (NOR)
Lower box: relay 1C | 3 | 4 |  |  | > | Cruise RC-1 | D19 Int 3 | D03 (NOR)
Panel Stop | 3 | 1 | White |  | > | Stop Button | D20 Int 4 | D02 (NOR)
Panel Cruise | 3 | 1 | Green |  | > | Cruise Button | D21 INT 5 | D03 (NOR)
Panel Blue switch | 3 | 1 | White-green |  | > | EnableSteer | D22 | D06
C1 LED | 3 | 1 | 6-Green | purple | < | LED 1 out | D23
Panel Red switch | 3 | 1 | White-orange |  | > | EnableBrake | D24 | D05
Motor controller reserved | 3 | 9 | 6-Red |  | < | Reverse | D25 | D07
Panel Green switch | 3 | 1 | Orange-white |  | > | EnableThrottle | D26 | D04
C3 LED | 3 | 1 | 6-Black | Blue | < | LED 3 out | D27
Panel Green LED | 3 | 1 | Green-white |  | < | CruiseLED | D28 | D08
C4 LED | 3 | 1 | 6-White | Green | < | LED 4 out | D29
Panel Red LED | 3 | 1 | White-blue |  | < | StopLED | D30 | D12
C5 LED | 3 | 1 | 7-Green | Yellow | < | LED 5 out | D31
Panel Reverse LED | 3 | 1 | Blue-white |  | < | Reverse LED | D32 | D13
C6 LED | 3 | 1 | 7-Red | Brown | < | LED 6 out | D33
Joystick reserved | 3 | 5 |  | Brown | > | Reverse button | D34 | D00
C7 LED | 3 | 1 | 7-Black | Gray | < | LED 7 out | D35
C1 Reserved: Reverse Cmd | 3 | 3 |  |  | > | Cruise Reverse | D36 | D01
C8 LED | 3 | 1 | 7-White | white | < | LED 8 out | D37
reserved | 3 | 0 |  |  |  |  | D38
reserved | 3 | 0 |  |  |  |  | D39
reserved | 3 | 0 |  |  |  |  | D40
reserved | 3 | 0 |  |  |  |  | D41
reserved | 3 | 0 |  |  |  | Unused | D42-D53
C1 Ground | 3 | 0 | Black | Black |  | Ground | J3:7 (Ground)
Joystick Ground | 3 | 5 | Black | Black |  | Ground | J3:7 (Ground) |  | black
Battery to relay board | 12 | 4 | Black | Red | > | 36 V | Relay 4B |  | White
Motor control | 9 | 4 | Black | Red | < | 36 V | Relay 4C |  | White
C1 5V | 7 | 3 | Red | Pink | > | 5 V | Servo Brake
C4-8 5V | 8 | 3 |  | Pink | < | +5 V | Servo Steer
C1 LED | 3,6 | 1 | 1-Green | purple | > | LED 1 in
C3 LED | 3,6 | 1 | 1-Black | Blue | > | LED 3 in
C4 LED | 3,6 | 1 | 1-White | Green | > | LED 4 in
C5 LED | 3,6 | 1 | 2-Green | Yellow | > | LED 5 in
C6 LED | 3,6 | 1 | 2-Red | Brown | > | LED 6 in
C7 LED | 3,6 | 1 | 2-Black | Gray | > | LED 7 in
C8 LED | 3,6 | 1 | 2-White | white | > | LED 8 in
Motor control 36V throttle | 9 | 1 |  | Red | > | 36 V fuel
Panel On switch | 2 | 1 | Black | orange | > | 12 v power |  |  | Brown
Joystick 5V | 7 or 8 | 5 | Red | Pink | > | 5 V |  |  | red
Battery Ground |  | 2 | Black | Black |  | Ground |  |  | Green
C4-8 Ground | 8 | 2 |  | Black |  | Ground
Motor control Ground |  | 2 |  | Black |  | Ground |  |  | black
Motor control throttle Ground |  | 2 |  | Black |  | Ground
Unspecified |  | 0
Panel |  | 1
Power distribution |  | 2
Arduino |  | 3
Relay |  | 4
Joystick |  | 5
Higher level computers |  | 6
Brake controller |  | 7
Steer controller |  | 8
Motor controller |  | 9
Shield |  | 10
Filter |  | 11
Battery |  | 12

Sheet: Power
End 1 | Connector 1 | Wire color | Connector 2 | Signal | End 2
758 A signal | Molex | White-blue | Molex | Motor current | A00
758 B signal | Molex | Green-white | Molex | Steer current | A01
758 C signal | Molex | White-orange | Molex | Brake current | A02
Relay ground | Screw ground | Black thin | Soldered | Brake ground | Brake servo ground
To D07 | Green | Yellow | Soldered | Brake PWM signal | Brake servo signal
Battery ground | Black | Black | Ring | Fuse ground | Fuse ground post
Brake ground | Black | Black | Spade | Fuse 5A Brake | Fuse tab brake
Motor control ground | Black | Black | Spade | Fuse 2A Motor | Fuse tab motor
Battery 12 V | Orange | Black | Soldered | 12 V | Panel: power switch
Panel: Power switch acc | tab | White | Ring | Switched 12 V | Panel: Post 12 V
C1 and C3 5V | Pink |  | Ring | Brake 5V | Panel: Post 5 V
Joystick 5V | Pink | Red | Ring | Brake 5V | Panel: Post 5 V
C1 and C3 ground | Black | Black | Ring | Brake ground | Panel: Post ground
Joystick ground | Black | Black | Ring | Brake ground | Panel: Post ground
758 power | Soldered |  | Ring | Brake 5V | Post 1
Brake servo 5V | Soldered | Red thin | Ring | Brake 5V | Post 1
Panel: Post 5 V | Ring | Red | Ring | Brake 5V | Post 1
Relay: 1B, 2B | Soldered | 2 red thin | Ring | Brake 5V | Post 1
758 ground | Soldered | Black | Ring | Brake ground | Post 10
Brake servo ground | Soldered | Black thin | Ring | Brake ground | Post 10
Panel: Post ground | Ring | Black | Ring | Brake ground | Post 10
Fuse 5A steer | Soldered | Black | Ring | Steer ground | Post 2
Steer servo ground | Soldered | Black thin | Ring | Steer ground | Post 2
Battery 36 V | Red | Black | Ring | 36 V | Post 3
Relay: 4B | Screw 4B | Black | Ring | 36 V | Post 3
Relay 4C | Screw 4C | Black | Ring | Relay 36 V | Post 4
758 A out | Soldered | Black | Ring | Motor control 36 V | Post 4
758 A in | Soldered | Black | Ring | Relay 36 V | Post 5
Motor control 36 V | Red | Black | Ring | Motor control 36 V | Post 5
Steer servo 12 V | Soldered | Red thick | Ring | Steer 12 V | Post 6
758 C in | Soldered | Red | Ring | Switched 12 V | Post 6
758 C out | Soldered | Red | Ring | Steer 12 V | Post 8
Panel: Post 12 V | Ring | Green | Ring | Switched 12 V | Post 8
758 B out | Soldered | Red | Ring | Brake 12 V | Post 8
758 B in | Soldered | Red | Ring | Switched 12 V | Post 9
Brake servo 12 V | Soldered | Red thick | Ring | Brake 12 V | Post 9
Relay power | Screw 12 V | Green | Ring | Brake 12 V | Post 9
To D02 | Gray | Green | Screw 1C | Cruise RC-1 | Relay 1C
To D03 | White | White | Screw 2C | Stop RC-2 | Relay 2C
C4 … C8 5V | Pink | Red thin | Soldered | Steer 5V | Steer servo 5 V
C4 … C8 ground | Black | Black thin | Soldered | Steer ground | Steer servo ground
To D06 | Yellow | Yellow | Soldered | Steer PWM signal | Steer servo signal

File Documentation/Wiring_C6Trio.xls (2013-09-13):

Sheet: C6 Navigator
Src/Dest | Dir | Signal | SGNL | Mega | C5
 |  | Front sonar range | F_RNG | A00
 |  | Front-left range | FL_RNG | A01
 |  | Front-right range | FR_RNG | A02
 |  | Left sonar range | L_RNG | A03
 |  | Right sonar range | R_RNG | A04
C2:7 | > | Cruise Brake | CRS_BRK | A05
C2:6 | > | Cruise Steer | CRS_STR | A06
C2:5 | > | Cruise Throttle | CRS_THR | A07
 |  | 2Front sonar range | F2RNG | A08
 |  | 2Front-left range | FL2RNG | A09
 |  | 2Front-right range | FR2RNG | A10
 |  | 2Left sonar range | L2RNG | A11
 |  | 2Right sonar range | R2RNG | A12
C3:A0 |  | Speed | SPEED | A13
C3:A1 |  | Spare | 4D5_6A14 | A14
 |  | Spare | 4D6_6A15 | A15
Serial Monitor in | > | Vision in | VIS_IN | D00 (Rx0, D0 PWM)
Serial Monitor out | < | Vision out | VIS_OUT | D01 (Tx0, D1 PWM)
Cylclometer | > | Odometer click | CLICK1 | D02 Int 0
 |  | Click2 | CLICK2 | D03 Int 1
C2:4;C3:12 | > | Move OK | MOV_OK | D04
 |  | Cruise Brake | CRS_BRK | D05 PWM)
 |  | Cruise Steer | CRS_STR | D06 PWM)
GPS J-11 2 |  | Spare | C6D7 | D07 PWM)
GPS J-11 5 |  | GPS LED1 | LED1 | D08
GPS J-11 6 |  | GPS Power | GPS_PWR | D09
Shield:D10 |  | Chip Select | C6D10 | D10
Shield:D11 |  | MOSI | MOSI | D11
Shield:D12 |  | MISO | MISO | D12
Shield:D13 |  | CLK | SCK | D13
GPS J-11 7, Rx | < | GPS control | GPS_CNTRL | D14 TX3
GPS J-11 8, Tx | > | GPS Location | GPS_LOC | D15 Rx3
C4:0 | < | Navigation Fix | NAV_FIX | D16 Tx2
C4:3 | > | C2 Status | C2STAT | D17 Rx2
INU:Rx | < | INU control | INU_CNTRL | D18 Int 2, Tx1
INU:Tx | > | INU Bearing | INU_BRN | D19 Int 3, Rx1
GPS J-11 3 |  | GPS_PPS | GPS_PPS | D20 Int 4
GPS J-11 4 |  | GPS LED2 | LED8 | D21 INT 5
 |  | LED7 | LED7 | D22
 |  | C6 Data Available | C6AVL | D23
 |  | LED6 | LED6 | D24
 |  | Vin | VIN | D25
 |  |  | DRV_CMD | D26, unused
 |  | INU Chip select | INU_SS | D27
 |  | Path | PATH | D28, unused
 |  | Spare | C6D29 | D29
 |  | Reset | RESET | D30, unused
 |  | Spare | C6D31 | D31
 |  |  | GND | D32, unused
 |  | Spare | C6D33 | D33
 |  | C4 Data available | C4AVL | D34
 |  | Spare | C6D35 | D35
 |  | Chaining 2 | CHN2 | D36
 |  | Spare | C6D37 | D37
 |  | Chaining 1 | CHN1 | D38
C2:D39 |  | Spare | D39 | D39
 |  | Cruise Brake | CRS_BRK | D40,D05
C2:D41 |  | Spare | D41 | D41
 |  | Cruise Steer | CRS_STR | D42,D06
 |  | Spare | 4D7_6D43 | D43
 |  | Power to sonar | PWR_SEL | D44
 |  | Cruise Throttle | CRS_THR | D45 (PWM)
 |  | Cruise Reverse | CRS_REV | D46
optical odometer |  | Mouse NPD | NPD | D47
 |  | Cruise Throttle | CRS_THR | D48,D45
optical odometer |  | Mouse LED | LED5 | D49 LED
optical odometer |  |  | MISO | D50 MISO
optical odometer |  |  | MOSI | D51 MOSI
optical odometer |  |  | SCK | D52 SCK
optical odometer |  | Mouse SS | MOUSE_SS | D53 SS
 |  |  |  | Vcc

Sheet: C7 Vision
Src/Dest | Wire color | Connector Color | Dir | Signal | Mega | Source pin
C4:9 |  |  | > | Expected horizontal | A00
C4:10 |  |  | > | Expected vertical | A01
C4:11 |  |  | > | Expected size | A02
 |  |  |  |  | A03
 |  |  |  |  | A04
 |  |  |  |  | A05
 |  |  |  |  | A06
 |  |  |  |  | A07
 |  |  |  |  | A08
 |  |  |  |  | A09
 |  |  |  |  | A10
 |  |  |  |  | A11
 |  |  |  |  | A12
 |  |  |  |  | A13
 |  |  |  |  | A14
 |  |  |  |  | A15
Web cam |  | USB | > | Camera | D00 (Rx0, D0 PWM)
Web cam |  | USB | < | Camera control | D01 (Tx0, D1 PWM)
 |  |  |  |  | D02 Int 0
 |  |  |  |  | D03 Int 1
C4:A0 |  |  | < | Horizontal | D04
C4:A1 |  |  | < | Vertical | D05 PWM)
C4:A2 |  |  | < | Size | D06 PWM)
C4:A3 |  |  | < | Coneness | D07 PWM)
 |  |  |  |  | D08
 |  |  |  |  | D09
 |  |  |  |  | D10
 |  |  |  |  | D11
 |  |  |  |  | D12
 |  |  |  |  | D13
 |  |  |  |  | D14 TX3
 |  |  |  |  | D15 Rx3
 |  |  |  |  | D16 Tx2
 |  |  |  |  | D17 Rx2
 |  |  |  |  | D18 Int 2
 |  |  |  |  | D19 Int 3
 |  |  |  |  | D20 Int 4
 |  |  |  |  | D21 INT 5
 |  |  |  |  | D22-D53
 |  |  |  |  | P0 Reset
 |  |  |  |  | P1 3V3
 |  |  |  |  | P2 5V
 |  |  |  |  | P3 Gnd
 |  |  |  |  | P4 Gnd
 |  |  |  |  | P5 Vin

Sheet: C4 Path
Src/Dest | Dir | Signal | SGNL | 2009 | Nano
C3:0 | < | Path | PATH | D01 J1:2 (Tx0) | L01
C6:16 | > | Navigation fix | NAV_FIX | D00 J1:1 (Rx0) | L02
 |  | Reset | RESET | RST | L03
 |  | Ground | GND | GND J3:7 | L04
C6:17 | > | C6 Data available | C6AVL | D02 J1:3 (INT0) | L05
C3:2 | < | C4 Data available | C4AVL | D03 J1:4 (INT1, PWM) | L06
 |  | Move OK | MOV_OK | D04 J1:5 | L07
 | < | Spare | 4D5_6A14 | D05 J1:6 (PWM) | L08
 | < | Spare | 4D6_6A15 | D06 J1:7 (PWM) | L09
 |  | Spare | 4D7_6D43 | D07 J1:8 | L10
 |  | Spare | D41 | D08 J3:1 | L11
 | < |  | SPD_LMT | D09 J3:2 (PWM) | L12
 |  | Spare | D39 | D10 J3:3 (PWM, SS) | L13
 |  |  |  | D11 J3:4 (PWM, MOSI) | L14
 |  |  |  | D12 J3:5 (MISO) | L15
 |  |  | VIN | VIN | R01
 |  | Ground | GND | GND | R02
 |  | Reset | RESET | RST | R03
 |  | 5 Volts | +5V | 5V | R04
F-3 | > | Front sonar range | F_RNG | A0 J2:1 | R05
FL-3 | > | Front-left range | FL_RNG | A1 J2:2 | R06
FR-3 | > | Front-right range | FR_RNG | A2 J2:3 | R07
 | > | Left sonar range | L_RNG | A3 J2:4 | R08
 | > | Right sonar range | R_RNG | A4 J2:5 | R09
 | > |  | F2RNG | A5 J2:6 | R10
 | > |  | L2RNG | A6 | R11
 | > |  | R2RNG | A7 | R12
 |  |  | AREF | AREF J3:8 | R13
 |  | 3.3 volts | 3.3V | 3.3V | R14
 |  |  | LED4 | D13 J3:6 (SCK, LED) | R15

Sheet: C5 Reverse
Src/Dest | Dir | Signal | SGNL | 2009 | Nano | MEGA
 | < |  | DRV_CMD | D01 J1:2 (Tx0) | L01 | D26, unused
C4:1 | > | Path | PATH | D00 J1:1 (Rx0) | L02 | D28, unused
 |  |  | RESET | RST | L03 | D30, unused
 |  |  | GND | GND J3:7 | L04 | D32, unused
C4:3 | > | C4 Data available | C4AVL | D02 J1:3 (INT0) | L05 | D34
 | < |  | CHN2 | D03 J1:4 (INT1, PWM) | L06 | D36
 | > | Chaining | CHN1 | D04 J1:5 | L07 | D38
C2:A10,C6:A10 | < | Cruise Brake | CRS_BRK | D05 J1:6 (PWM) | L08 | D40,D05
C2:A11,C6:A11 | < | Cruise Steer | CRS_STR | D06 J1:7 (PWM) | L09 | D42,D06
Relay | < | Power to sonar | PWR_SEL | D07 J1:8 | L10 | D44
 | < | Cruise Reverse | CRS_REV | D08 J3:1 | L11 | D46
C2:A9, C6:A9 | < | Cruise Throttle | CRS_THR | D09 J3:2 (PWM) | L12 | D48,D45
C2:4;C6:23 | > | Move OK | MOV_OK | D10 J3:3 (PWM, SS) | L13 | D50 (MISO)
 | < |  | SPEED | D11 J3:4 (PWM, MOSI) | L14 | D52 (SCK)
D41 |  | Spare | D41 | D12 J3:5 (MISO) | L15 | D54 (GND)
 |  |  | VIN | VIN | R01
 |  |  | GND | GND | R02
 |  |  | RESET | RST | R03
 |  |  | +5V | 5V | R04
 | > |  | F2RNG | A0 J2:1 | R05
 | > |  | FL2RNG | A1 J2:2 | R06
 | > |  | FR2RNG | A2 J2:3 | R07
 | > |  | L2RNG | A3 J2:4 | R08
 | > |  | R2RNG | A4 J2:5 | R09
 |  |  | F_RNG | A5 J2:6 | R10
 |  |  | L_RNG | A6 | R11
 |  |  | R_RNG | A7 | R12
 |  |  | AREF | AREF J3:8 | R13
 |  |  | 3.3V | 3.3V | R14
 |  |  | LED5 | D13 J3:6 (SCK, LED) | R15

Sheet: C3 Pilot
Src/Dest | Dir | Signal | SGNL | 2009 | Nano
 | < |  | DRV_CMD | D01 J1:2 (Tx0) | L01
C4:1 | > | Path | PATH | D00 J1:1 (Rx0) | L02
 |  |  | RESET | RST | L03
 |  |  | GND | GND J3:7 | L04
C4:3 | < | C4 Data available | C4AVL | D02 J1:3 (INT0) | L05
 | > |  | CHN2 | D03 J1:4 (INT1, PWM) | L06
 | < | Chaining | CHN1 | D04 J1:5 | L07
C2:A10,C6:A10 | < | Cruise Brake | CRS_BRK | D05 J1:6 (PWM) | L08
C2:A11,C6:A11 | < | Cruise Steer | CRS_STR | D06 J1:7 (PWM) | L09
Relay | < | Power to sonar | PWR_SEL | D07 J1:8 | L10
 | < | Cruise Reverse | CRS_REV | D08 J3:1 | L11
C2:A9, C6:A9 | < | Cruise Throttle | CRS_THR | D09 J3:2 (PWM) | L12
C2:4;C6:23 | > | Move OK | MOV_OK | D10 J3:3 (PWM, SS) | L13
 | < |  | SPEED | D11 J3:4 (PWM, MOSI) | L14
D39 |  | Spare | D39 | D12 J3:5 (MISO) | L15
 |  |  | VIN | VIN | R01
 |  |  | GND | GND | R02
 |  |  | RESET | RST | R03
 |  |  | +5V | 5V | R04
F-3 | > | Front sonar range | F_RNG | A0 J2:1 | R05
FL-3 | > | Front-left range | FL_RNG | A1 J2:2 | R06
FR-3 | > | Front-right range | FR_RNG | A2 J2:3 | R07
 | > | Left sonar range | L_RNG | A3 J2:4 | R08
 | > | Right sonar range | R_RNG | A4 J2:5 | R09
 | > |  | F2RNG | A5 J2:6 | R10
 | > |  | L2RNG | A6 | R11
 | > |  | R2RNG | A7 | R12
 |  |  | AREF | AREF J3:8 | R13
 |  |  | 3.3V | 3.3V | R14
 | < |  | LED3 | D13 J3:6 (SCK, LED) | R15
 |  |  |  | P0 Reset
 |  |  |  | P1 3V3
F-1 | < | Select Tx / chaining |  | P2 5V
F-4 | < | Enable ranging |  | P2 5V
F-6 | < | Vcc |  | P2 5V
FL-1 | < | Select Tx / chaining |  | P2 5V
FL-4 | < | Enable ranging |  | P2 5V
FL-6 | < | Vcc |  | P2 5V
FR-1 | < | Select Tx / chaining |  | P2 5V
FR-4 | < | Enable ranging |  | P2 5V
FR-6 | < | Vcc |  | P2 5V
F-7 |  | Ground |  | P3 Gnd
FL-7 |  | Ground |  | P3 Gnd
FR-7 |  | Ground |  | P3 Gnd
(none) |  |  |  | P4 Gnd
(none) |  |  |  | P5 Vin
(none) |  |  |  | P6 (none)
F-0 |  | (none)
F-2 | > | Pulse width
F-5 | > | Tx serial out
FL-0 |  | (none)
FL-2 | > | Pulse width
FL-5 | > | Tx serial out
FR-0 |  | (none)
FR-2 | > | Pulse width
FR-5 | > | Tx serial out

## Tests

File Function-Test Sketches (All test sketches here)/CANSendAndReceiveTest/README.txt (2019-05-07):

Librarys for Can_Due:

due_can.h, .cpp
https://github.com/atlas0fd00m/CanCat/tree/master/ext_libs/due_can

(this one Might not be needed, possibly included in existing library)
"variant.h, .cpp   
https://github.com/arduino/ArduinoCore-samd/tree/master/variants/arduino_zero

----------------------------------------------------
Librarys for Can_Mega

mcb_can.h, .cpp  (CanBus Shield)
https://github.com/Seeed-Studio/CAN_BUS_Shield

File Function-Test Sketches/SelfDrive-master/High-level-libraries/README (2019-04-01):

Links to Addition Libaries NEEDED from Adafruit! 

Adafruit_GPS -> https://github.com/adafruit/Adafruit_GPS
Adafruit_Sensor -> https://github.com/adafruit/Adafruit_Sensor

* I2C must modify "Wire" to "Wire1" in the cpp file use SCL1 and SDA1 (with pullup resistor) for Arduino Due  
Adafruit_L3GD20 (Triple Axis Gyroscope) -> https://github.com/adafruit/Adafruit_L3GD20
Adafruit_LSM303 (Accelerometer + Magnetometer) -> https://github.com/adafruit/Adafruit_LSM303DLHC

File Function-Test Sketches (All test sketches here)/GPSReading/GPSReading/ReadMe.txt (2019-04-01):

GPSReading.ino is nothing than reading current geo coordinates to let you how GPS works

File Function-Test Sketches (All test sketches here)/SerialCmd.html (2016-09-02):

Serial commands

There are two formats for the keyword. Those starting with '$' are comma separated values, followed by a checksum. Commands starting with a character other than '$' have arguments grouped by braces into keywords and values. The former may be used with instruments; the latter is the format used for interprocessor communication.

DRIVE

GameBots serial command format allows replacement by the USARSim simulator. Since USARsim is no longer available, the Gamebots format has been modified:

1. D {s ComandedSpeed} {a ComandedSteerAngle}

Where:

{s ComandedSpeed} ComandedSpeed is an intege giving the speed for the rear wheel in centimeters per second.

The value is the speed, in centimeters / second.

{a ComandedSteerAngle} ComandedSteerAngle is an integer that specifies the steer angle

of Elcano’s front wheels. The value is the absolute steer angle, in degrees.

Example: D {s 259} {a -3}

SENSOR

A similar format will be used for sensed information from C6.

2. S {s ActualSpeed}

ActualSpeed gives the speed for the rear wheel.

The value is the speed, in centimeters per second.

Other sensors are:

3. S {a Deg}

Steering angle of the front wheels, in degrees times.

0 degrees is straight ahead, small positive numbers are degrees to the right.

Negative numbers (mod 360) are degrees to the left.

4. S {p EPosMeters,NPosMeters} {b Deg}

// Best estimate of vehicle position, fused from all sensors.

The East and North positions are relative to the origin.

Bearing tells which way the vehicle is pointing.

OTHER

5. G {n Num} {p EPosMeters,NPosMeters} {b Deg}

5a. G {n Num} {p EPosMeters,NPosMeters} {b Deg} {r Probability}

6. X {n Num} {p EPosMeters,NPosMeters} {b Deg} {s SegSpeed}

Goal gives the positions of the cones, which may be updated from visual information. The next goal is always {Num 1} If a bearing is present, it is the desired direction of approach to the goal.

The localization processor passes messages 4, SENSOR and 5, GOAL to the vision processor. The vision processor then computes the expected position of the cone in the image. After processing the image, it will compute an updated cone position, including the probability that a cone is present in the image. It passes message 5a back to the vision processor.

Segment 1 is the next desired position from the present position. These are followed by Segments 2, 3, 4, 5. Farther segments would not be transmitted. The speed on a segment is the recommended speed, taking account of conditions and turning radius.

GPS

NMEA Output sentences $GPxxx. These include $GPRMC, $GPVTG. $GPGGA, $GPGSA and $GPGSV. See http://www.adafruit.com/datasheets/GlobalTop-FGPMMOPA6H-Datasheet-V0A.pdf

Communication to the GPS receiver uses NMEA PMTK packets such as $PMTK220, $PMTK314 and $PMTK605. See http://www.adafruit.com/datasheets/PMTK_A08.pdf

Maps

Format is similar to NMEA output. '*xx' means the character '*' followed by a checksum.

$MAPLS,N*xx

Requests processor N to list the names of all maps.

$MAPTX,N,count,num,name*xx

Processor N transmits the name of map num of count. Count is the number of maps on the processor.

$MAPSL,N,name*xx

Request processor N to send contents of map 'name'.

$MAPLN,N,count,num,data*xx

Processor N sends line num of count for the requested map. 'Data' consists of

node,latitude,longitude,PositionEast,PositionNorth,Link1,Link2,Link3,Link4,Dist1,Dist2,Dist3,Dist4

Where

node is the name or number of the point.

latitude and longitude are in decimal degrees.

Positions are in meters

Links are other nodes that are directly linked to this node. If there are more than four, use two different names for the present node, but separate them by zero distance. If there are fewer than four, that field is blank.

Dist are distances in meters along the road to a node.

Example data:

8,47.760342,-122.189784,71.903,154.917,2,7,15,,268.441,142.961,269.358,

15,47.757929,-122.189467,95.599,-113.397,8,16,18,,269.358,26.369,182.216,

13,47.621921,-122.348628,170.313,69.008,14,,,,18.578,,,,

The maps themselves are internal to C4 and its SD card. They do not have to be transmitted. C4 needs to have additional information about the route. From this information, it will produce the next portion of the drive path, which will be transmitted to C3.

The map for the SD card must contain information about the links between nodes. Each link will have the following information:

$LNKLST,startNode,endNode,numberOfSegments,segmentIndex1,...,segmentIndexN

$LNKSEG,index,nextIndex,PositionEast,PositionNorth,bearing,width,speed

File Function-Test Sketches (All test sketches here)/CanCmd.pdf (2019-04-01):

The CANID starts from 0X00 to 0XFF
0X00 to 0X04 is reserved for E-Stop.
0X05 is reserved for DRIVE (speed and direction)
0X0A to 0X0C is reserved for SENSOR (actual speed and actual direction) 0X10 to 0X13 is reserved for Goal
0X20 is reserved for GPS

** Please be ware of the initial CAN-Bus baud rate. If you use MCP2515 module for testing, the baud rate needs to be set as twice as due CAN baud rate.

CAN Message Sample
{ID} {Lower 4 bytes} {Higher 4 bytes} eg. {0X00} {FFFFFFFF} {00000000}

DRIVE (CANID 0X05)
0X05 ComandedSpeed ComandedSteerAngle

ID 05 gives the command drive speed and angle.
ComandedSpeed: ComandedSpeed is an intege giving the speed for the rear wheel in centimeters per second.
The value is the speed, in centimeters / second.
ComandedSteerAngle: ComandedSteerAngle is a signed integer that specifies the steer angle (in degrees) of Elcano's front wheels. Negative value indicates left; positive value indicates right; 0 is straight.

eg. 05 256 -3 gives 05 00100000 FFFFFFFD

SENSOR
0X0A ActualSpeed ActualDeg

ID 0A gives the speed for the rear wheel in centimeters per second. And ActualDeg is angle of the front wheels, in degrees times.
0 degrees is straight ahead, small positive numbers are degrees to the right. Negative numbers (mod 360) are degrees to the left.

eg. 0A 100 0 gives 64000000 00000000

0X0B EPosMeters NPosMeters
0C Deg

Best estimate of vehicle position, fused from all sensors. The East and North positions are relative to the origin. Bearing tells which way the vehicle is pointing.

eg. 0B 200 200
0C 40

Goal
0X10 EPosMeters NPosMeters 0X11 Deg GoalCounter
0X13 Probability
0X15 SegSpeed

Goal gives the positions of the cones, which may be updated from visual information. The localization processor passes messages 4, SENSOR and 5, GOAL to the vision processor. The vision processor then computes the expected position of the cone in the image. After processing the image, it will compute an updated cone position, including the probability that a cone is present in the image. It passes message 5a back to the vision processor.
Each segment represents the next goal to move. All segments are stored in a FIFO queue and pop out one by one. The speed on a segment is the recommended speed, taking account of conditions and turning radius.

GPS

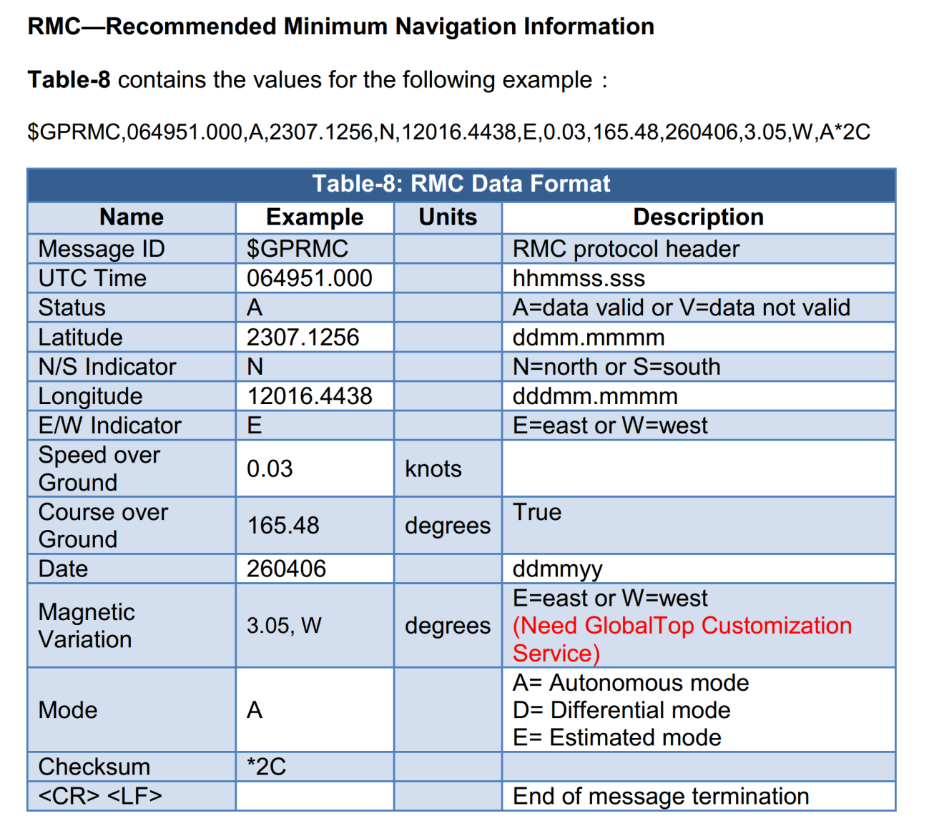
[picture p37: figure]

0X20 N/E (0/1) Latitude | Longitude
0X20 (0/1) (w maximum value 5F5E0FF) (w maximum value 3B9AC9FF)

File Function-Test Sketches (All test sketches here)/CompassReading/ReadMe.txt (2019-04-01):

CompassReading.ino is nothing than reading compass to let you how compass works

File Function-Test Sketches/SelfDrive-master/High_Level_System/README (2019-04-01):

This is the most updated High level System test with C6, C4 and C3 together. 
Make sure to also include the High-level-libraries when running this code.

Note: C4 is commented out because the A star algorithm still need further integration and testing.

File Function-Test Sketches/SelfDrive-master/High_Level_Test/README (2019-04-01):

This is the most updated version of the High level code with a mostly tested and working version of C6 and C3. 
Make sure to also include the High-level-libraries when running this code.

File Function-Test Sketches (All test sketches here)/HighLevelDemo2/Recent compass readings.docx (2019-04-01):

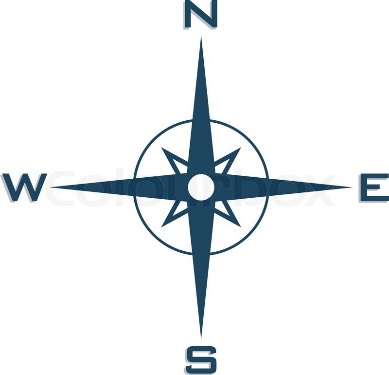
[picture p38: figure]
Image result for compass

Std:

N: 360

E: 90

S: 180

W:270

High 1:

N: 328.5 - 31.5

E: 2.5 - 98.5

S: 242.5 + 62.5

W:284.5 + 14.5

High 2:

N: 346 -14

E: 100.5 +10.5

S: 170 -10

W: 249 -21

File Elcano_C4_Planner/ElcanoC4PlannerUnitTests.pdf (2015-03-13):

# C4 Planner Unit Tests

## Framework

Tests for C4 Planner are written using the ArduinoUnit framework. Follow the instructions under “Getting Started” at https://github.com/mmurdoch/arduinounit/blob/master/readme.md to import this framework.

## Writing Unit Tests

If you're already familiar with how unit testing frameworks behave in general, you can probably skip this section. This is a primer on how to write effective unit tests.

Some things to keep in mind:
- Think about your upper and lower bounds and be sure to test outside them
- Don't worry about whether the scenario is realistic
- We're only testing the behavior of a function based on the input provided; we're not testing that it works properly with other systems
- If a test fails, that may be okay; just determine whether the scenario that failed is intended to be caught elsewhere. For example, in an embedded system we might assume correct input because we know another microcontroller is handling the verification and we'd rather have a quick response. Just ensure it's handled somewhere.

### How to approach writing unit tests

1. Select a function you would like to test and list out the inputs, output, and dependencies (other functions it calls, objects and variables it uses or updates, etc.)
2. Determine what the expected values are for each of the items listed in the first step and write a list of the values you would like to test. Some examples include:
- lowest expected value
- highest expected value
- zero
- a value below the lowest expected
- a value above the highest expected
- a combination of values that could cause overflow
- different types of strings (ASCII vs. Unicode)
- null
- empty objects
3. Start with tests that ensure it behaves as expected with the input that is expected (the "happy path" scenario)
4. Write one test for each change in expected behavior. For example, if you have a function that takes two variables as input, test the behavior with both variables within expected ranges, then start testing unexpected values with variable a while variable b remains in expected ranges, then b in unexpected ranges with a in expected ranges, and finally both outside expected ranges.
5. Run the tests as you go to make sure they're working as expected. Note:"as expected" means the behavior is what you would expect it to be given the input provided. If the input is bad, you might expect a garbage output, but that output should be predictable and should not cause a crash.
6. If a test fails when you expected it to pass, make sure it was written correctly, but don't assume the code functions properly just because it seems to work without problems; that's what unit tests are designed to catch.

### Troubleshooting

Tests Print Out Results Over and Over
This indicates there was something wrong with the tests that caused some kind of error or exception. Usually this is because data that is being accessed by the function isn't initialized.

How to Resolve
1. Comment and uncomment blocks of code to determine which function call is causing the error. If all tests are working correctly, the tests will run once and then stop (even though they're called from the loop).
2. Once you've isolated the function call, follow the logic and determine if any objects or variables are being called that are global or that were passed in. These are the most likely culprits.
3. Check the setup routine for the *.ino file being tested and see if there are any general setup routines being called that may be a dependency for your function.
4. In the unit test, be sure to initialize the values for the variables, structs, and objects being used by the function you're testing.
5. Rerun the test, and if it's still not working repeat steps 3 and 4 until the problem is found.

### Example unit tests

This code shows an example of a couple of unit tests on one of the Elcano_C4_Planner functions. More generic examples can be found on the ArduinoUnit page.

Note that these examples don't include tests where the function has a return value (yet). If you need to test a return value, create a variable to store the return value before you call the function. For example:

intexpected=0;
intactual=foo(bar);
assertEqual(actual,expected);

/*ConstructNetworktests

Inputs:junction*Map,intMapPoints Expectedvaluesfor*Map:arrayofjunctions ExpectedvaluesforMapPoints:MAP_POINTS

junctionvalues:
longeast_mm,longnorth_mm,intdestination[4],longDistance[4]

destinationistheindexofthegraphnodesthisjunctionhasanedgeto Distanceisthedistancemultiplierforeachdestinationnode

*/

//Happypathtestwithsmallmap //Verifiesthatthedistancesarecorrectlyupdatedinthemappassedto //thefunction.
test(ConstructNetwork_small)
{
intm=2;

//inputjunction
junctionactual[2]={
0, 0,1, END, END, END, 1,1,1,1, //0 3, 4,0, END, END, END, 1,1,1,1, //1

};

//expectedoutput
junctionexpected[2]={
0, 0,1, END, END, END, 5,1,1,1, //0 3, 4,0, END, END, END, 5,1,1,1, //1

};

//Callthefunctionbeingtested ConstructNetwork(actual,m);

//Verifythedatainthearraypassedtothefunctionisupdated //Becausewedon'thaveaprintoverloadforjunction,weneedto //makeassertationsonindividualpiecesofdatawithinthestruct. //Thesameappliestoarrays.
for(inti=0;i<2;i++)
{
assertEqual(actual[i].east_mm,expected[i].east_mm); assertEqual(actual[i].north_mm,expected[i].north_mm); for(intj=0;j<4;j++){
assertEqual(actual[i].destination[j],expected[i].destination[j]); assertEqual(actual[i].Distance[j],expected[i].Distance[j]);
}

}
}

//Happypathtestwithlargemap //Verifiesthatthedistancesarecorrectlyupdatedinthemappassedto //thefunction.
test(ConstructNetwork_large)
{
intm=100;
//inputjunction
junctionactual[100]={
0, 0,1, | 2, | 3, | 4, 1,1,1,1, //0
3, 4,0, END, END, END, 1,1,1,1, //1 3, 4,0, END, END, END, 1,1,1,1, //2 0, 0,0, END, END, END, 1,1,1,1, //3 3, 4,0, END, END, END, 1,1,1,1, //4 };

//expectedoutput
junctionexpected[100]={
0, 0,1, | 2, | 3, | 4, 5,5,0,5, //0
3, 4,0, END, END, END, 5,1,1,1, //1 3, 4,0, END, END, END, 5,1,1,1, //2 0, 0,0, END, END, END, 0,1,1,1, //3 3, 4,0, END, END, END, 5,1,1,1, //4 };

//Callthefunctionbeingtested ConstructNetwork(actual,m);

//Verifythedatainthearraypassedtothefunctionisupdated //Becausewedon'thaveaprintoverloadforjunction,weneedto //makeassertationsonindividualpiecesofdatawithinthestruct. //Thesameappliestoarrays.
for(inti=0;i<m;i++)
{
assertEqual(actual[i].east_mm,expected[i].east_mm); assertEqual(actual[i].north_mm,expected[i].north_mm); for(intj=0;j<4;j++){
assertEqual(actual[i].destination[j],expected[i].destination[j]); assertEqual(actual[i].Distance[j],expected[i].Distance[j]);
}
}
}

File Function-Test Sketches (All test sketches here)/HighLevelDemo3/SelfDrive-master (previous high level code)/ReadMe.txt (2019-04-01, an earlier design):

The selfDrive-master is high level code wrote by previous capstone team. The algo still working but they use Elcano serial instead of CAN bus.

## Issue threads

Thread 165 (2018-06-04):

History rewritten on 3-June-2018

ptressel, 2018-06-04:
We found that we'd accidentally committed 3rd party (Arduino) libraries to the repository, and had also included large media files (images, videos) that don't need revision control.  These have all been stripped out.  (Many thanks to the authors of git filter-branch...)  The prior version of the repository is available temporarily at https://github.com/elcano/old_elcano.  When we're certain we have what we need out of the non-master branches there, it will be removed.

Folks with new code or changes to existing files will need to patch those in to the new repo.

TylerFolsom, 2018-06-04:
Pat -Thanks for taking care of this.  Next step is to put current code into the new repo. How do you recommend I do so?- Tyler

-------- Original Message --------
Subject: [elcano/elcano] History rewritten on 3-June-2018 (#165)
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

ptressel, 2018-06-05:
If you want to add new versions of existing files, or entire new files, then the easiest way is:  Rename your local copy of the old repo, and clone a fresh copy of elcano/elcano.  It's fine to use the master branch for this.  Copy the new / updated files that you want to go together in a single commit into the appropriate places the new clone.  Commit those as usual -- use a nice, informative commit message ;-).  Repeat for each set of files that belong together in a commit.  Once you have all the new / updated files added, then you'll need to overwrite your own TylerFolsom/elcano fork of the elcano repo (not the main elcano/elcano repo).  I just checked -- it looks like you don't have new material there, and there are no branches other than master, so it should be safe to overwrite it.  The only difference in the push command is that you'll need to add the "--force" option.  If you want me to have a look before you do this, let me know.

ptressel, 2018-06-05:
Conor and Joe may be interested in a git fixing session, if you want to do the various git work as a group.

Closed 2019-06-14.

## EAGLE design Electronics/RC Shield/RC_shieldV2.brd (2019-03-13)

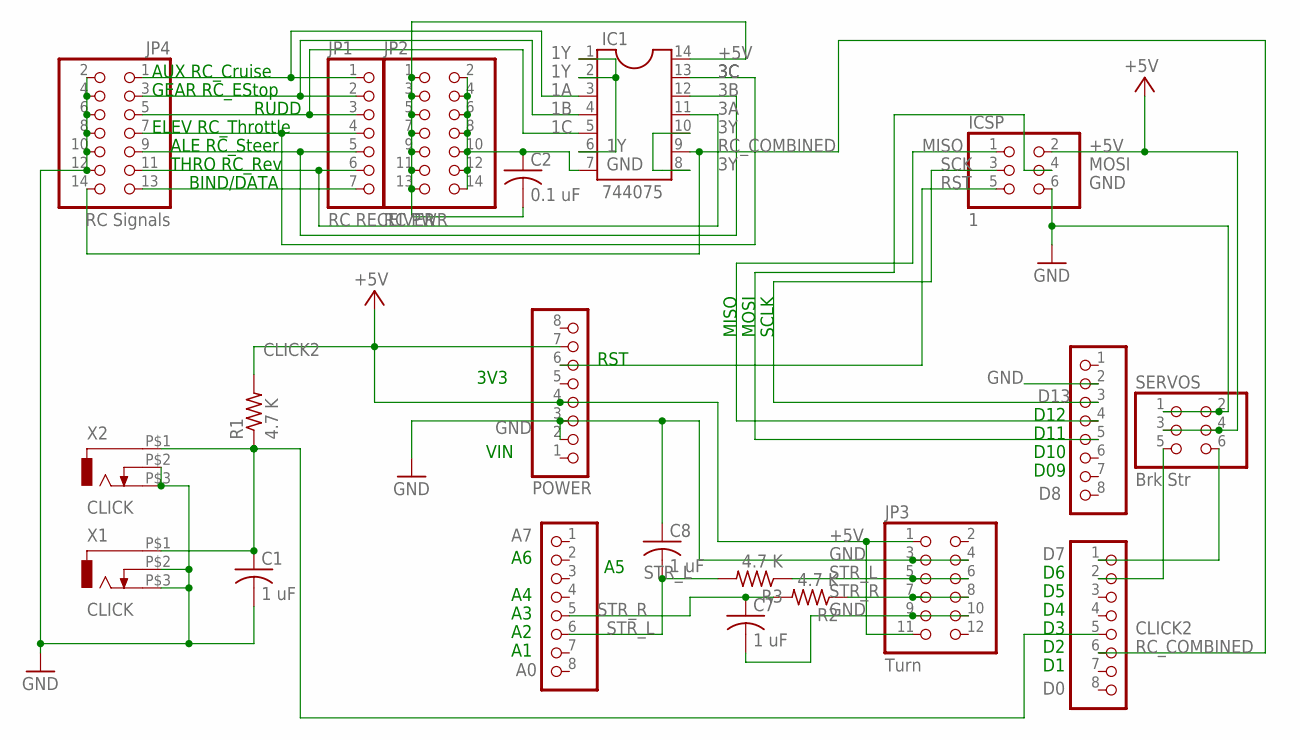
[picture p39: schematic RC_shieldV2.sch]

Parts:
A0: A7; 1X08
C1, C7, C8: 1 uF; C025-030X050
C2: 0.1 uF; C025-030X050
D0: D7; 1X08
D8: D13; 1X08
IC1: 744075; DIL14
ICSP: 1; 2X03
JP1: RC RECEIVER; 1X07
JP2: RC PWR; 2X07
JP3: Turn; 2X06
JP4: RC Signals; 2X07
POWER: GND; 1X08
R1, R2, R3: 4.7 K; 0207/10
SERVOS: Brk Str; 2X03
X1, X2: CLICK; ODO_JACK

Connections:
1A: IC1.3, JP1.1, JP4.1
1B: IC1.4, JP1.2, JP4.3
1C: IC1.5, JP1.3, JP4.5
1Y: IC1.1, IC1.2, IC1.6
3A: IC1.11, JP1.6, JP4.11
3B: IC1.12, JP1.5, JP4.9
3C: IC1.13, JP1.4, JP4.7
3Y: IC1.8, IC1.10
+5V: C2.2, IC1.14, ICSP.2, JP2.1, JP2.3, JP2.5, JP2.7, JP2.9, JP2.11, JP2.13, JP3.1, JP3.11, POWER.4, POWER.7, R1.2, SERVOS.3, SERVOS.4
CLICK2: C1.1, D0.5, R1.1, X1.P$1 (1), X2.P$1 (1)
GND: C1.2, C2.1, C7.2, C8.1, D8.2, IC1.7, ICSP.6, JP2.2, JP2.4, JP2.6, JP2.8, JP2.10, JP2.12, JP2.14, JP3.3, JP3.4, JP3.9, JP3.10, JP4.2, JP4.4, JP4.6, JP4.8, JP4.10, JP4.12, POWER.2, POWER.3, SERVOS.1, SERVOS.2, X1.P$2 (2), X1.P$3 (3), X2.P$2 (2), X2.P$3 (3)
MISO: D8.4, ICSP.1
MOSI: D8.5, ICSP.4
unnamed: JP3.7, JP3.8, R2.1
unnamed: JP3.5, JP3.6, R3.1
unnamed: JP1.7, JP4.13
unnamed: D0.2, SERVOS.5
unnamed: D0.1, SERVOS.6
RC_COMBINED: D0.6, IC1.9, JP4.14
RST: ICSP.5, POWER.6
SCK: D8.3, ICSP.3
STR_L: A0.6, C8.2, R3.2
STR_R: A0.5, C7.1, R2.2

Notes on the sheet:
D10
D11
D12
D09
VIN
MISO
MOSI
SCLK
RST
3V3
AUX RC_Cruise
GEAR RC_EStop
RUDD
ELEV RC_Throttle
ALE RC_Steer
THRO RC_Rev
BIND/DATA

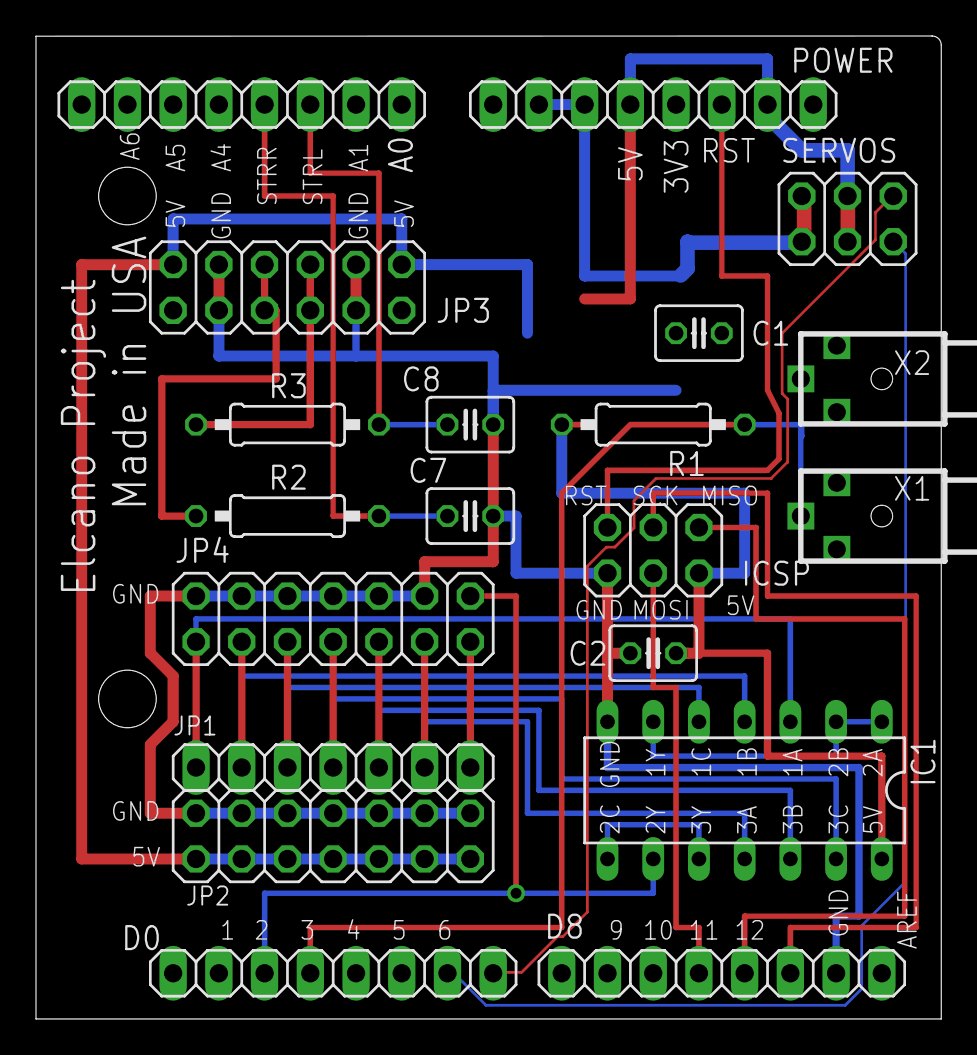
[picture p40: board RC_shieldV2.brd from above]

Board: 2 copper layers, 50.3 x 54.6 mm, 20 parts (0 on the bottom side), 23 nets.

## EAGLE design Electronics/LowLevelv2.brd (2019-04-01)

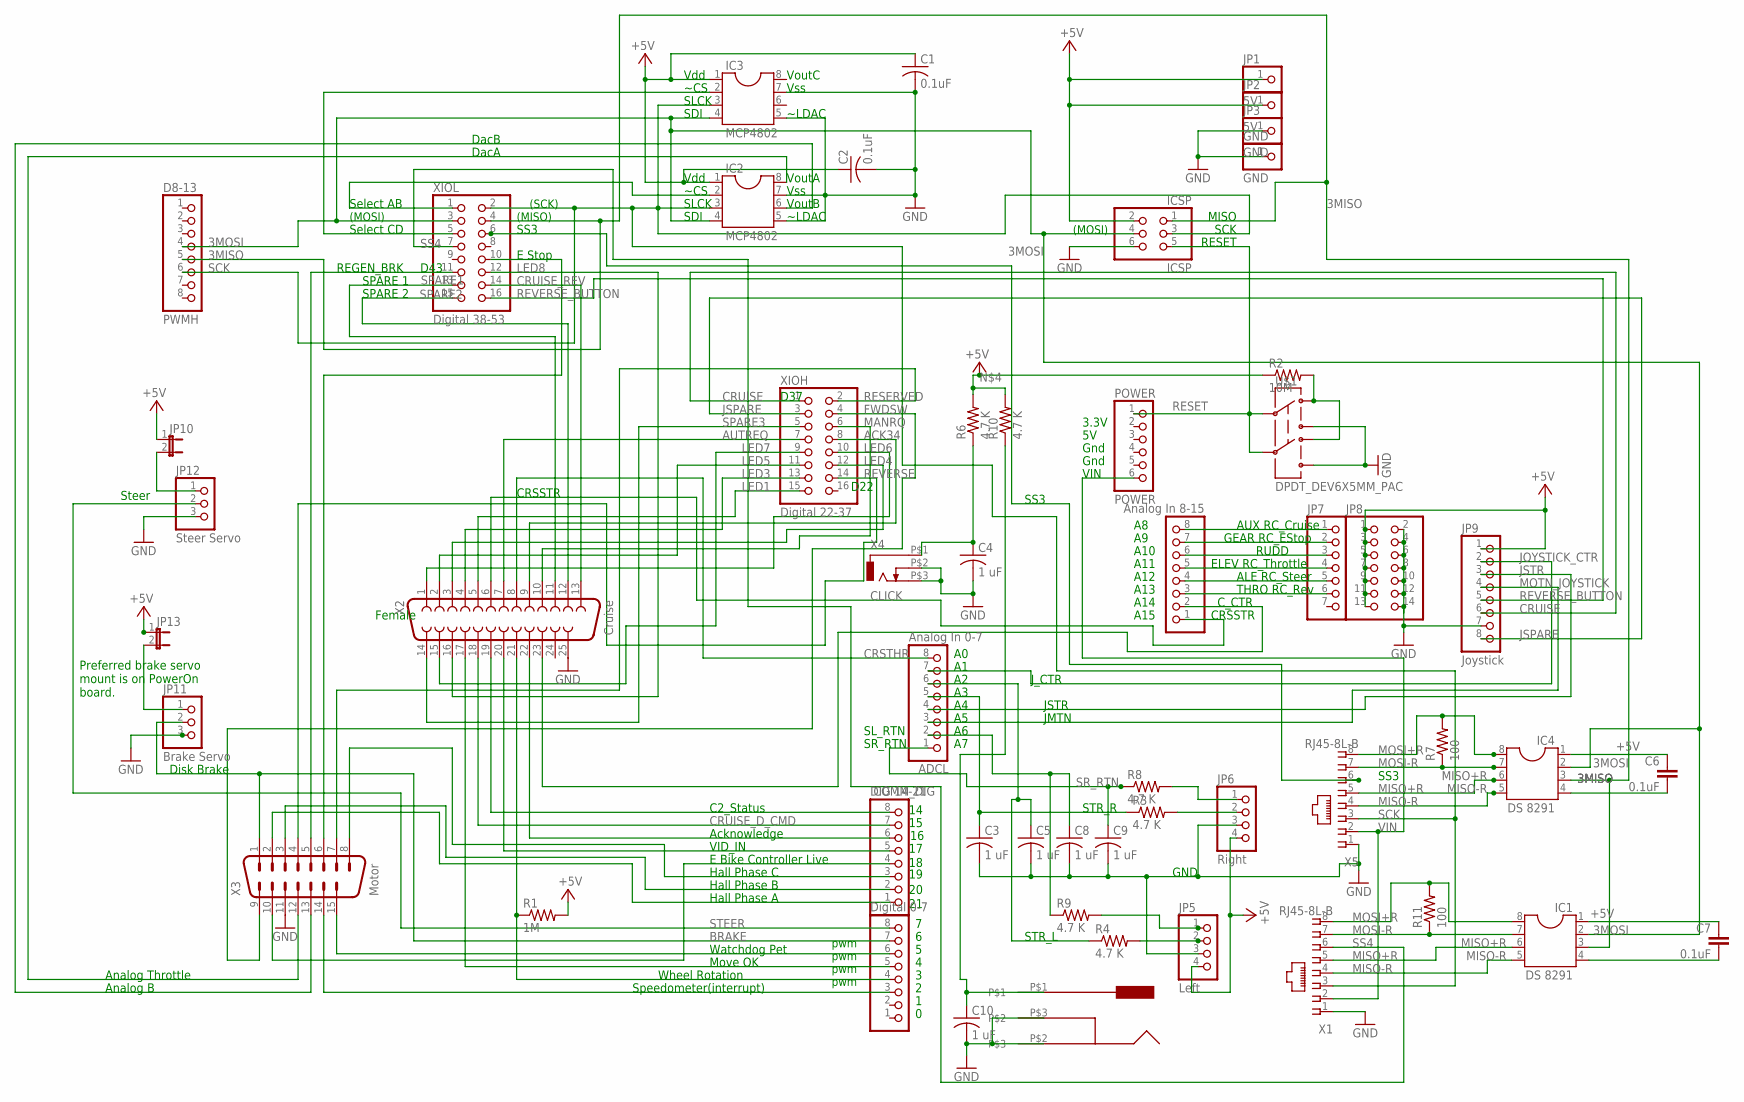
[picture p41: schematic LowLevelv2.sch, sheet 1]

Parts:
ADCH: Analog In 8-15; 1X08
ADCL: Analog In 0-7; 1X08
C1, C2: 0.1uF; C025-025X050
C3, C4, C5, C8, C9, C10: 1 uF; C025-030X050
C6, C7: 0.1uF; C2.5-2
COMM_DIG: DIG 14-21; 1X08
D8-13: PWMH; 1X08
GND: GND; 1X01
IC1, IC4: DS 8291; DIL08
IC2, IC3: MCP4802; DIL08
ICSP: ICSP; 2X03
JP1, JP2: 5V; 1X01
JP3: GND; 1X01
JP5: Left; 1X04/90
JP6: Right; 1X04/90
JP7: PINHD-1X7; 1X07
JP8: PINHD-2X7; 2X07
JP9: Joystick; 1X08/90
JP10, JP13: JP1E; JP1
JP11: Brake Servo; 1X03/90
JP12: Steer Servo; 1X03/90
POWER: POWER; 1X06
PWML: Digital 0-7; 1X08
R1: 1M; 0207/10
R2: 10M; 0207/10
R3, R4, R6, R8, R9, R10: 4.7 K; 0207/10
R7, R11: 100; 0207/10
U$1: DPDT_DEV6X5MM_PAC; NEWSWITCH2_PAC
U$2: CUI_JACKTHROUGH_HOLE; CUIJACK
X1, X5: RJ45-8L-B; RJ45-NO-SHIELD
X2: Cruise; F25H
X3: Motor; 182-015-MALE
X4: CLICK; ODO_JACK
XIOH: Digital 22-37; 2X08
XIOL: Digital 38-53; 2X08

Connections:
1C: ADCH.6, JP7.3
3A: ADCH.3, JP7.6
3MISO: D8-13.5, IC1.3, IC4.3, ICSP.1, XIOL.4
3MOSI: D8-13.4, IC1.2, IC2.4, IC3.4, IC4.2, ICSP.4, XIOL.3
5V: JP10.2, JP12.1
5VOLT: JP11.1, JP13.2
+5V: C1.1, C2.1, C6.1, IC2.1, IC3.1, IC4.1, ICSP.2, JP1.1, JP2.1, JP5.4, JP6.4, JP8.1, JP8.3, JP8.5, JP8.7, JP8.9, JP8.11, JP8.13, JP9.1, JP10.1, JP13.1, R1.2, R2.1, R6.2, R10.2
A14: ADCH.7, JP7.2
A15: ADCH.8, JP7.1
ACK34: X2.9, XIOH.8
ACKNOWLEDGE: COMM_DIG.6, X2.22
AUTREQ: X2.7, XIOH.7
BRAKE: JP11.2, PWML.7, X3.1
C2STATUS: COMM_DIG.8, X2.19
CRSSTR: ADCH.1, X2.6
CRSTHR: ADCL.8, X2.8
CRUISE: JP9.6, XIOH.1
CRUISE_D_CMD: COMM_DIG.7, X2.18
CRUISE_REV: X2.13, XIOL.14
C_CTR: ADCH.2, X2.23
DACA: IC2.8, X3.12
DACB: IC2.6, X3.13
EBIKECONTRL: COMM_DIG.4, X3.10
ESTOP: X3.6, XIOL.10
FWDSW: X3.9, XIOH.4
GND: C1.2, C2.2, C3.2, C4.2, C5.2, C8.2, C9.2, C10.2, GND.1, IC2.5, IC2.7, IC3.5, IC3.7, ICSP.6, JP3.1, JP5.3, JP6.3, JP8.2, JP8.4, JP8.6, JP8.8, JP8.10, JP8.12, JP8.14, JP9.7, JP11.3, JP12.3, U$1.PIN3 (3), U$1.PIN6 (6), U$2.P$2, U$2.P$3, X1.1, X2.25, X3.11, X4.P$2 (2), X4.P$3 (3), X5.1
HALLPHASEA: COMM_DIG.1, X3.2
HALLPHASEB: COMM_DIG.2, X3.3
HALLPHASEC: COMM_DIG.3, X3.8
JOYSTICK_CTR: ADCL.7, JP9.2
JSPARE: JP9.8, XIOH.3
JSTR: ADCL.4, JP9.3
LED1: X2.5, XIOH.15
LED3: X2.4, XIOH.13
LED4: X2.3, XIOH.12
LED5: X2.2, XIOH.11
LED6: X2.1, XIOH.10
LED7: X2.15, XIOH.9
LED8: X2.16, XIOL.12
L_STR: JP5.2, R4.2
MANRQ: X2.10, XIOH.6
MISO+R: IC1.6, IC4.6, X1.5, X5.5
MISO-R: IC1.5, IC4.5, X1.4, X5.4
MOSI+R: IC1.8, IC4.8, R7.2, R11.2, X1.8, X5.8
MOSI-R: IC1.7, IC4.7, R7.1, R11.1, X1.7, X5.7
MOTN_JOYSTICK: ADCL.3, JP9.4
MOVEOK: PWML.5, X2.17
unnamed: C10.1, R10.1, U$2.P$1
unnamed: C6.2, IC4.4
unnamed: C7.2, IC1.4
unnamed: C4.1, R6.1, X4.P$1 (1)
unnamed: C7.1, IC1.1
unnamed: R2.2, U$1.PIN1 (1), U$1.PIN4 (4)
unnamed: ADCH.4, JP7.5
unnamed: ADCH.5, JP7.4
REGENBAKE: X3.5, XIOL.11
RESERVED: X3.7, XIOH.2
RESET: ICSP.5, POWER.1, U$1.PIN2 (2), U$1.PIN5 (5)
REVERSE: X3.4, XIOH.14
REVERSE_BUTTON: JP9.5, XIOL.16
R_STR: JP6.2, R3.2
SCK: D8-13.6, IC2.3, IC3.3, ICSP.3, X1.3, X5.3, XIOL.2
SELECTAB: IC2.2, XIOL.1
SELECTCD: IC3.2, XIOL.5
SL_RET: JP5.1, R9.2
SL_RTN: ADCL.2, C8.1, R9.1
SPARE1: X2.11, XIOL.13
SPARE2: X2.12, XIOL.15
SPARE3: X2.14, XIOH.5
SPEEDOMETER: PWML.3, X3.14
SR_RET: JP6.1, R8.2
SR_RTN: ADCL.1, C9.1, R8.1
SS3: X5.6, XIOL.6
SS4: X1.6, XIOL.7
STEER: JP12.2, PWML.8
STR_L: ADCL.6, C5.1, R4.1
STR_R: ADCL.5, C3.1, R3.1
VIDIN: COMM_DIG.5, X2.20
VIN: POWER.6, X1.2, X5.2
WATCHDOG: PWML.6, X3.15
WHEELROTATION: PWML.4, R1.1, X2.21

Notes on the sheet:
(MOSI)
pwm
(SCK)
(MISO)
Move OK
Disk Brake
Gnd
Steer
Acknowledge
VID_IN
C2_Status
REGEN_BRK
Female
Vdd
~CS
SLCK
VoutA
Vss
VoutB
~LDAC
VoutC
Select AB
Select CD
Watchdog Pet
Analog B
Analog Throttle
SDI
DacA
DacB
D43
3.3V
MISO
SCK
RESET
VIN
Wheel Rotation
Speedometer(interrupt)
AUX RC_Cruise
RUDD
ELEV RC_Throttle

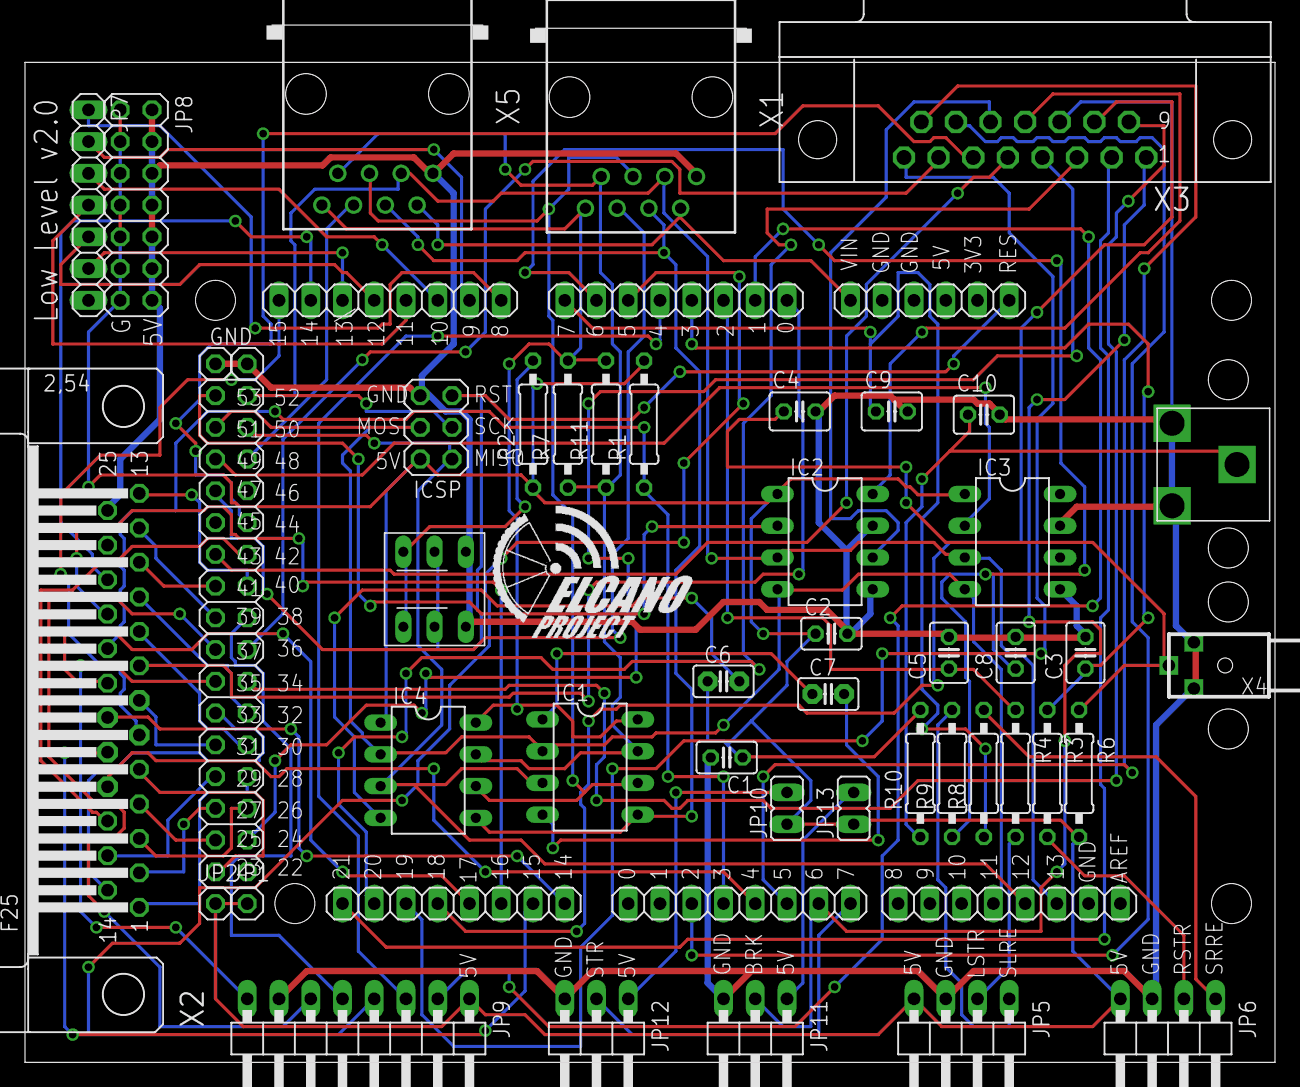
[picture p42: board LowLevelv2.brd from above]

Board: 2 copper layers, 100.0 x 83.0 mm, 53 parts (0 on the bottom side), 81 nets.

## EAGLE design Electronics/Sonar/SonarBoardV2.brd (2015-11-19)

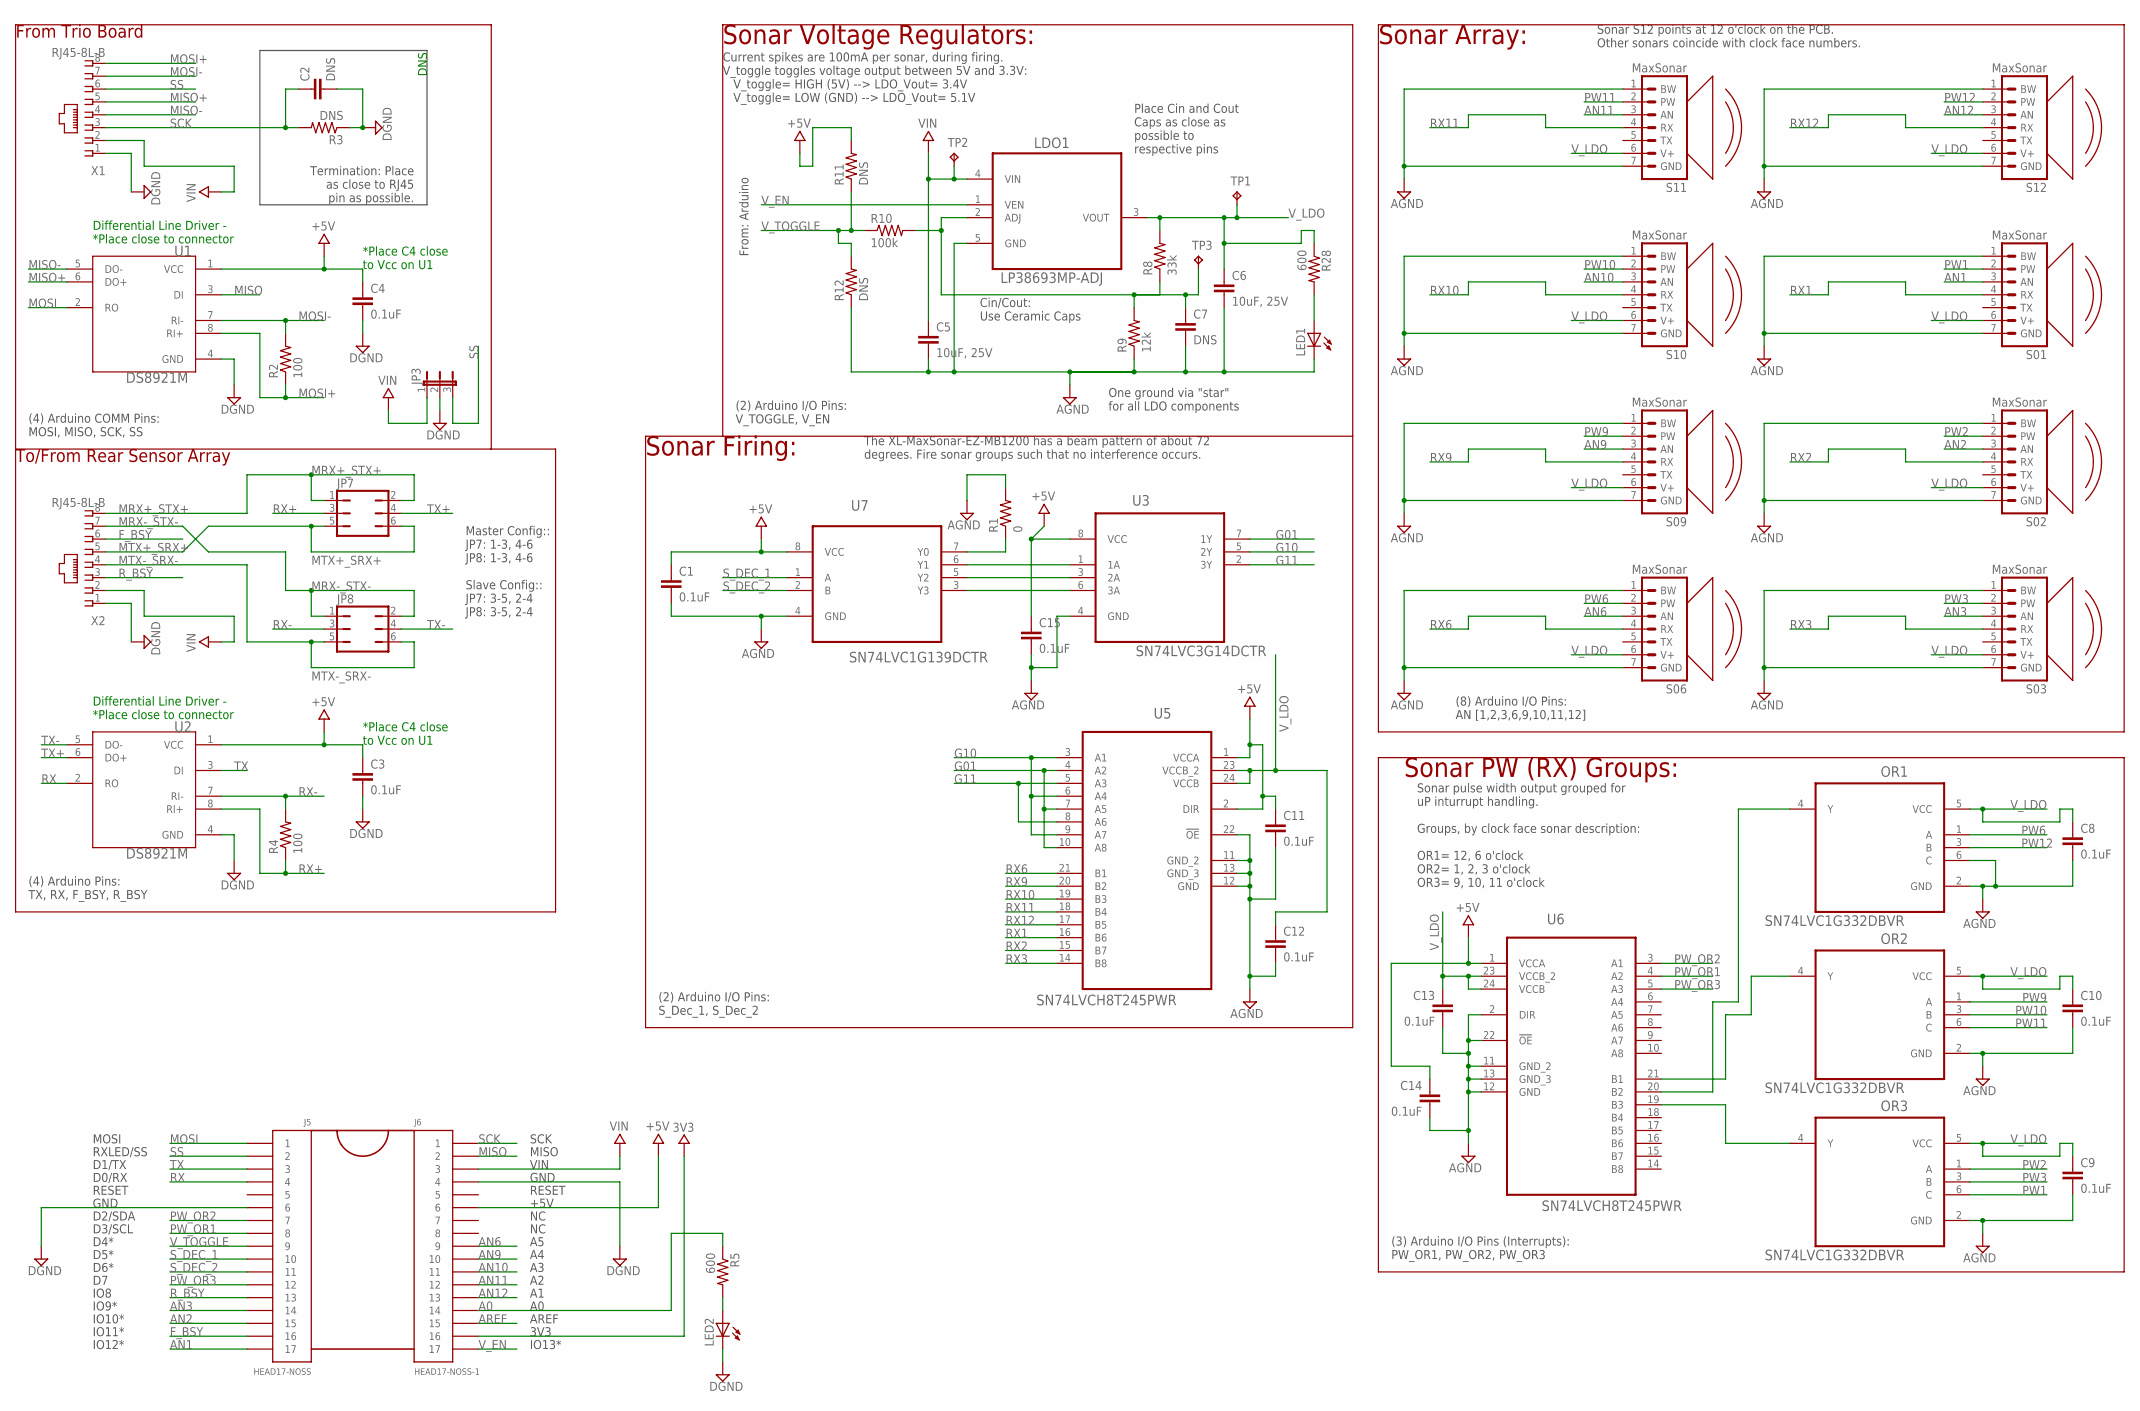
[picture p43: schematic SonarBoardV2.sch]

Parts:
C1, C3, C4, C8, C9, C10, C11, C12, C13, C14, C15: 0.1uF; 0603-CAP
C2, C7: DNS; 0603-CAP
C5, C6: 10uF, 25V; 0805
J5: HEAD17-NOSS
J6: HEAD17-NOSS-1
JP3: JP2E; JP2
JP7, JP8: JP3Q
LDO1: LP38693MP-ADJ; SOT150P696X180-5N
LED1, LED2: LEDSML0603; SML0603
OR1, OR2, OR3: SN74LVC1G332DBVR; SOT95P280X145-6N
R1: 0; 0603-RES
R2, R4: 100; R0805
R3, R11, R12: DNS; 0603-RES
R5, R28: 600; 0603-RES
R8: 33k; 0603-RES
R9: 12k; 0603-RES
R10: 100k; 0603-RES
S01, S02, S03, S06, S09, S10, S11, S12: MaxSonar; XL-MAXSONAR-PACKAGE
TP1, TP2, TP3: TPPAD1-17; P1-17
U1, U2: DS8921M; SOIC127O620X175-8N
U3: SN74LVC3G14DCTR; SOP65P400X130-8N
U5, U6: SN74LVCH8T245PWR; SOP65P640X120-24N
U7: SN74LVC1G139DCTR; SOP65P400X130-8N@1
X1, X2: RJ45-8L-B; RJ45-NO-SHIELD

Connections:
3V3: J6.16
+5V: C1.1, C3.1, C4.1, C11.1, C14.1, C15.1, J6.6, R11.2, U1.1 (VCC), U2.1 (VCC), U3.8 (VCC), U5.1 (VCCA), U5.2 (DIR), U6.1 (VCCA), U7.8 (VCC)
A0: J6.14, R5.1
AN1: J5.17, S01.3 (AN)
AN2: J5.15, S02.3 (AN)
AN3: J5.14, S03.3 (AN)
AN6: J6.9, S06.3 (AN)
AN9: J6.10, S09.3 (AN)
AN10: J6.11, S10.3 (AN)
AN11: J6.12, S11.3 (AN)
AN12: J6.13, S12.3 (AN)
AREF: J6.15
F_BSY: J5.16, X2.6
G01: U3.7 (1Y), U5.4 (A2), U5.7 (A5), U5.10 (A8)
G10: U3.5 (2Y), U5.3 (A1), U5.6 (A4), U5.9 (A7)
G11: U3.2 (3Y), U5.5 (A3), U5.8 (A6)
GND: C1.2, C2.2, C3.2, C4.2, C5.2, C6.2, C7.2, C8.2, C9.2, C10.2, C11.2, C12.2, C13.2, C14.2, C15.2, J5.6, J6.4, JP3.2, LDO1.5 (GND), LED1.C, LED2.C, OR1.2 (GND), OR1.6 (C), OR2.2 (GND), OR3.2 (GND), R1.2, R3.1, R9.1, R12.1, S01.1 (BW), S01.7 (GND), S02.1 (BW), S02.7 (GND), S03.1 (BW), S03.7 (GND), S06.1 (BW), S06.7 (GND), S09.1 (BW), S09.7 (GND), S10.1 (BW), S10.7 (GND), S11.1 (BW), S11.7 (GND), S12.1 (BW), S12.7 (GND), U1.4 (GND), U2.4 (GND), U3.4 (GND), U5.11 (GND_2), U5.12 (GND), U5.13 (GND_3), U5.22 (!OE), U6.2 (DIR), U6.11 (GND_2), U6.12 (GND), U6.13 (GND_3), U6.22 (!OE), U7.4 (GND), X1.1, X2.1
MISO: J6.2, U1.3 (DI)
MISO+: U1.6 (DO+), X1.5
MISO-: U1.5 (DO-), X1.4
MOSI: J5.1, U1.2 (RO)
MOSI+: R2.1, U1.8 (RI+), X1.8
MOSI-: R2.2, U1.7 (RI-), X1.7
MRX+_STX+: JP7.1, JP7.2, X2.8
MRX-_STX-: JP8.1, JP8.2, X2.7
MTX+_SRX+: JP7.5, JP7.6, X2.5
MTX-_SRX-: JP8.5, JP8.6, X2.4
unnamed: LED2.A, R5.2
unnamed: LED1.A, R28.2
unnamed: U3.1 (1A), U7.6 (Y1)
unnamed: U3.3 (2A), U7.5 (Y2)
unnamed: U3.6 (3A), U7.3 (Y3)
unnamed: R1.1, U7.7 (Y0)
unnamed: OR1.4 (Y), U6.20 (B2)
unnamed: OR2.4 (Y), U6.21 (B1)
unnamed: OR3.4 (Y), U6.19 (B3)
PW1: OR3.6 (C), S01.2 (PW)
PW2: OR3.1 (A), S02.2 (PW)
PW3: OR3.3 (B), S03.2 (PW)
PW6: OR1.1 (A), S06.2 (PW)
PW9: OR2.1 (A), S09.2 (PW)
PW10: OR2.3 (B), S10.2 (PW)
PW11: OR2.6 (C), S11.2 (PW)
PW12: OR1.3 (B), S12.2 (PW)
PW_OR1: J5.8, U6.4 (A2)
PW_OR2: J5.7, U6.3 (A1)
PW_OR3: J5.12, U6.5 (A3)
RX: J5.4, U2.2 (RO)
RX1: S01.4 (RX), U5.16 (B6)
RX2: S02.4 (RX), U5.15 (B7)
RX3: S03.4 (RX), U5.14 (B8)
RX6: S06.4 (RX), U5.21 (B1)
RX9: S09.4 (RX), U5.20 (B2)
RX10: S10.4 (RX), U5.19 (B3)
RX11: S11.4 (RX), U5.18 (B4)
RX12: S12.4 (RX), U5.17 (B5)
RX+: JP7.3, R4.1, U2.8 (RI+)
RX-: JP8.3, R4.2, U2.7 (RI-)
R_BSY: J5.13, X2.3
SCK: C2.1, J6.1, R3.2, X1.3
SS: J5.2, JP3.3, X1.6
S_DEC_1: J5.10, U7.1 (A)
S_DEC_2: J5.11, U7.2 (B)
TX: J5.3, U2.3 (DI)
TX+: JP7.4, U2.6 (DO+)
TX-: JP8.4, U2.5 (DO-)
VIN: C5.1, J6.3, JP3.1, LDO1.4 (VIN), TP2.TP, X1.2, X2.2
V_ADJ: C7.1, LDO1.2 (ADJ), R8.1, R9.2, R10.2, TP3.TP
V_EN: J6.17, LDO1.1 (VEN)
V_LDO: C6.1, C8.1, C9.1, C10.1, C12.1, C13.1, LDO1.3 (VOUT), OR1.5 (VCC), OR2.5 (VCC), OR3.5 (VCC), R8.2, R28.1, S01.6 (V+), S02.6 (V+), S03.6 (V+), S06.6 (V+), S09.6 (V+), S10.6 (V+), S11.6 (V+), S12.6 (V+), TP1.TP, U5.23 (VCCB_2), U5.24 (VCCB), U6.23 (VCCB_2), U6.24 (VCCB)
V_TOGGLE: J5.9, R10.1, R11.1, R12.2

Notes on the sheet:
Sonar S12 points at 12 o'clock on the PCB. Other sonars coincide with clock face numbers.
Termination: Place as close to RJ45 pin as possible.
From Trio Board
Differential Line Driver - *Place close to connector
*Place C4 close to Vcc on U1
DNS
To/From Rear Sensor Array
The XL-MaxSonar-EZ-MB1200 has a beam pattern of about 72 degrees. Fire sonar groups such that no interference occurs.
Sonar Voltage Regulators:
Place Cin and Cout Caps as close as possible to respective pins
One ground via "star" for all LDO components
Current spikes are 100mA per sonar, during firing. V_toggle toggles voltage output between 5V and 3.3V: V_toggle= HIGH (5V) --> LDO_Vout= 3.4V V_toggle= LOW (GND) --> LDO_Vout= 5.1V
Cin/Cout: Use Ceramic Caps
From: Arduino
Sonar Firing:
Sonar Array:
(2) Arduino I/O Pins: S_Dec_1, S_Dec_2
(2) Arduino I/O Pins: V_TOGGLE, V_EN
(8) Arduino I/O Pins: AN [1,2,3,6,9,10,11,12]
Sonar PW (RX) Groups:
Sonar pulse width output grouped for uP inturrupt handling. Groups, by clock face sonar description: OR1= 12, 6 o'clock OR2= 1, 2, 3 o'clock OR3= 9, 10, 11 o'clock
(3) Arduino I/O Pins (Interrupts): PW_OR1, PW_OR2, PW_OR3
(4) Arduino COMM Pins: MOSI, MISO, SCK, SS
Master Config:: JP7: 1-3, 4-6 JP8: 1-3, 4-6 Slave Config:: JP7: 3-5, 2-4 JP8: 3-5, 2-4
(4) Arduino Pins: TX, RX, F_BSY, R_BSY
MOSI
RXLED/SS
D1/TX
D0/RX
RESET
GND
D2/SDA
D3/SCL
D4*
D5*
IO8
D6*
IO9*
IO10*
IO11*

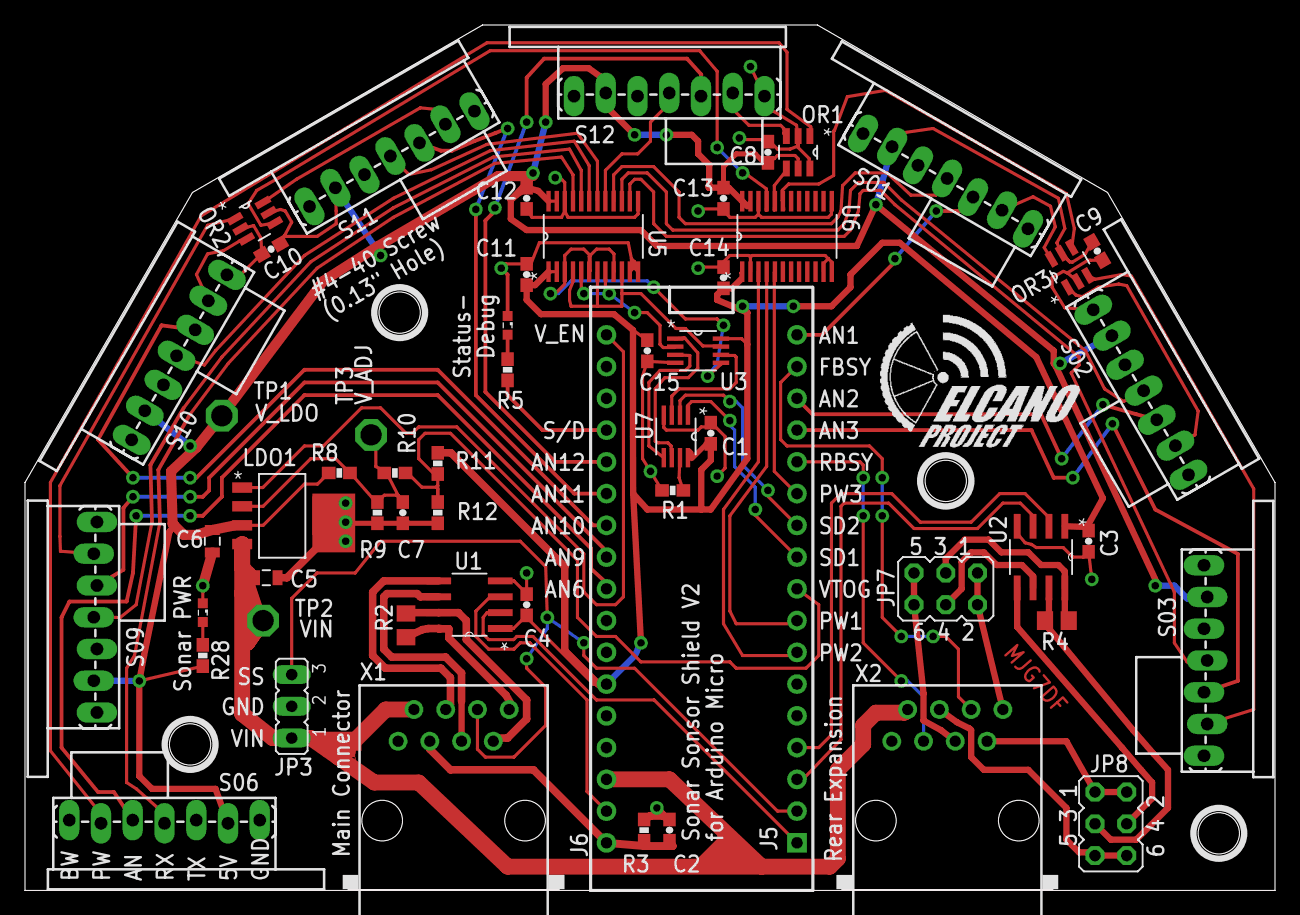
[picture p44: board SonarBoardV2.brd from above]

Board: 2 copper layers, 100.0 x 69.2 mm, 60 parts (0 on the bottom side), 69 nets.

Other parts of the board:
U$15, U$16, U$17, U$18: STAND-OFF

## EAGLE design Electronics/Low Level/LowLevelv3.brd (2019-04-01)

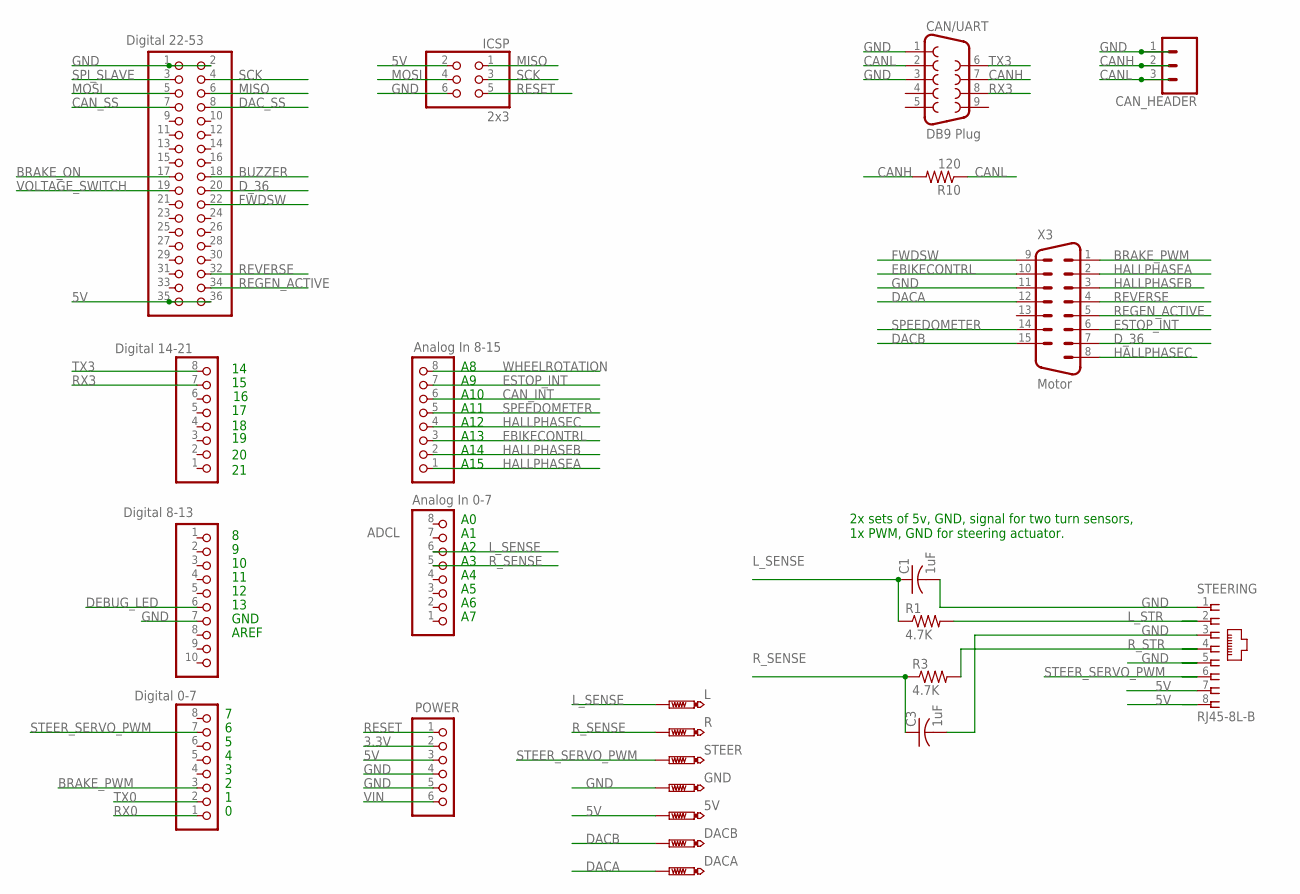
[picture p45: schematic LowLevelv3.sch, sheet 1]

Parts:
5V: PTR1PAD1-17; P1-17
ADCH: Analog In 8-15; 1X08
ADCL: Analog In 0-7; 1X08
C1, C3: 1uF; C1206
CAN/UART: DB9 Plug; DB9
CAN_HEADER: CONN_03-SCREW-5MM; SCREWTERMINAL-5MM-3
DACA: PTR1PAD1-17; P1-17
DACB: PTR1PAD1-17; P1-17
DIGITAL_0-7: Digital 0-7; 1X08
DIGITAL_8-13: Digital 8-13; 1X10
DIGITAL_14-21: Digital 14-21; 1X08
GND: PTR1PAD1-17; P1-17
ICSP: 2x3; 2X03
L: PTR1PAD1-17; P1-17
MEGA_EXPANSION: Digital 22-53; PINHEAD_2X18
POWER: PINHD-1X6; 1X06
R: PTR1PAD1-17; P1-17
R1, R3: 4.7K; R1206
R10: 120; R1206
STEER: PTR1PAD1-17; P1-17
STEERING: RJ45-8L-B; RJ45-NO-SHIELD
X3: Motor; 182-015-MALE

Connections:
3.3V: POWER.2
5V: 5V.TP, ICSP.2, MEGA_EXPANSION.35, MEGA_EXPANSION.36, POWER.3, STEERING.7, STEERING.8; also elsewhere on the board
BRAKE_ON: MEGA_EXPANSION.17; also elsewhere on the board
BRAKE_PWM: DIGITAL_0-7.3, X3.1
BUZZER: MEGA_EXPANSION.18; also elsewhere on the board
CANH: CAN/UART.7, CAN_HEADER.2, R10.2; also elsewhere on the board
CANL: CAN/UART.2, CAN_HEADER.3, R10.1; also elsewhere on the board
CAN_INT: ADCH.6; also elsewhere on the board
CAN_SS: MEGA_EXPANSION.7; also elsewhere on the board
DACA: DACA.TP, X3.12; also elsewhere on the board
DACB: DACB.TP, X3.15; also elsewhere on the board
DAC_SS: MEGA_EXPANSION.8; also elsewhere on the board
DEBUG_LED: DIGITAL_8-13.6; also elsewhere on the board
D_36: MEGA_EXPANSION.20, X3.7
EBIKECONTRL: ADCH.3, X3.10
ESTOP_INT: ADCH.7, X3.6; also elsewhere on the board
FWDSW: MEGA_EXPANSION.22, X3.9
GND: C1.2, C3.2, CAN/UART.1, CAN/UART.3, CAN_HEADER.1, DIGITAL_8-13.7, GND.TP, ICSP.6, MEGA_EXPANSION.1, MEGA_EXPANSION.2, POWER.4, POWER.5, STEERING.1, STEERING.3, STEERING.5, X3.11; also elsewhere on the board
HALLPHASEA: ADCH.1, X3.2
HALLPHASEB: ADCH.2, X3.3
HALLPHASEC: ADCH.4, X3.8
L_SENSE: ADCL.6, C1.1, L.TP, R1.1
L_STR: R1.2, STEERING.2
MISO: ICSP.1, MEGA_EXPANSION.6; also elsewhere on the board
MOSI: ICSP.4, MEGA_EXPANSION.5; also elsewhere on the board
REGEN_ACTIVE: MEGA_EXPANSION.34, X3.5
RESET: ICSP.5, POWER.1; also elsewhere on the board
REVERSE: MEGA_EXPANSION.32, X3.4
RX0: DIGITAL_0-7.1
RX3: CAN/UART.8, DIGITAL_14-21.7
R_SENSE: ADCL.5, C3.1, R.TP, R3.1
R_STR: R3.2, STEERING.4
SCK: ICSP.3, MEGA_EXPANSION.4; also elsewhere on the board
SPEEDOMETER: ADCH.5, X3.14
SPI_SLAVE: MEGA_EXPANSION.3
STEER_SERVO_PWM: DIGITAL_0-7.7, STEER.TP, STEERING.6
TX0: DIGITAL_0-7.2
TX3: CAN/UART.6, DIGITAL_14-21.8
VIN: POWER.6
VOLTAGE_SWITCH: MEGA_EXPANSION.19; also elsewhere on the board
WHEELROTATION: ADCH.8; also elsewhere on the board

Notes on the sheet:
A10
A11
A12
A13
A14
A15
GND
AREF
2x sets of 5v, GND, signal for two turn sensors, 1x PWM, GND for steering actuator.

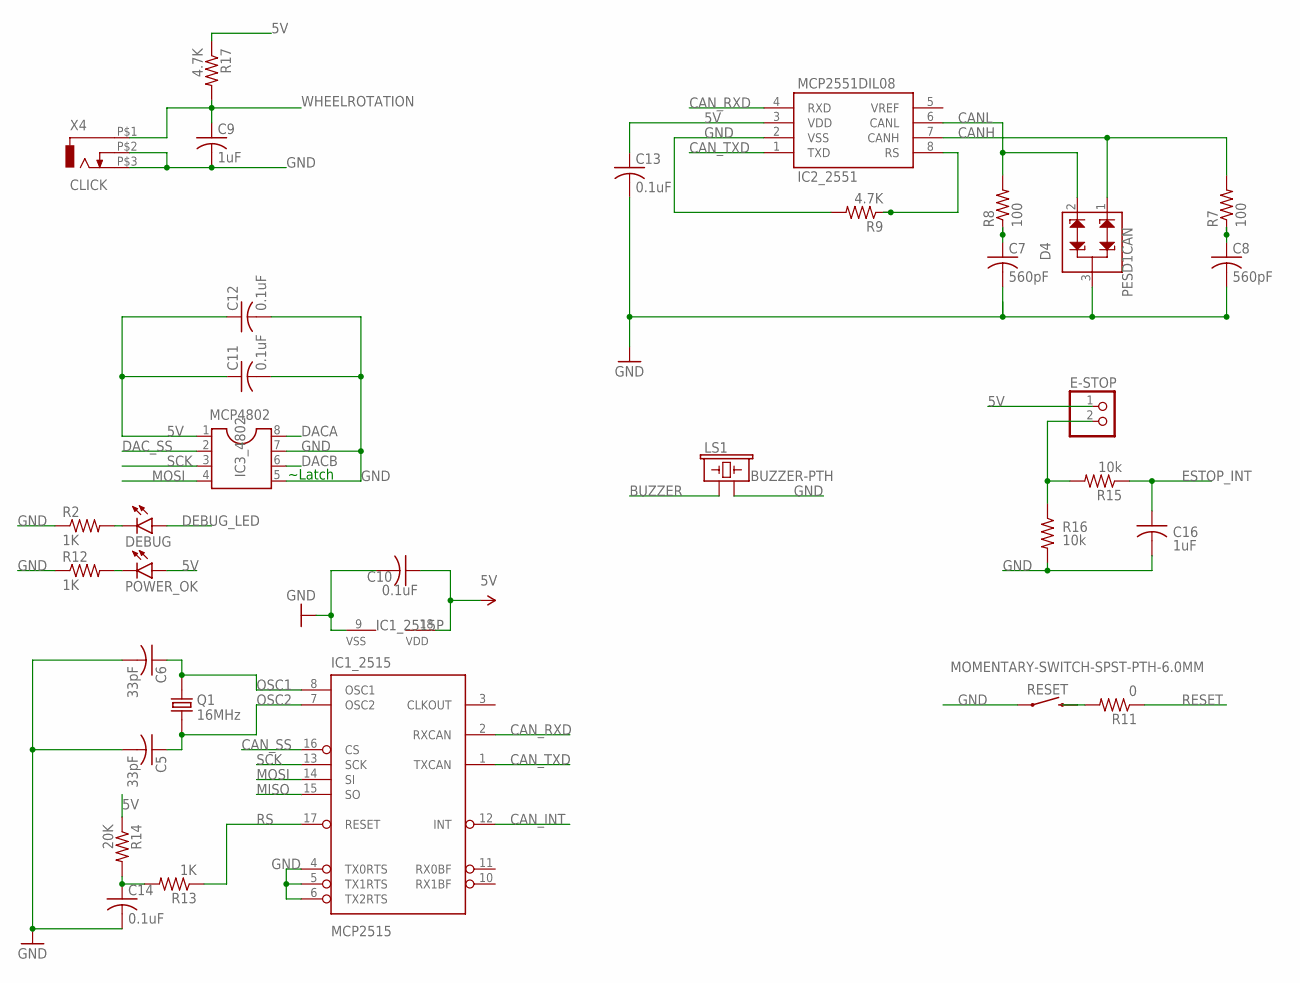
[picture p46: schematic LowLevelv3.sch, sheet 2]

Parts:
C5, C6: 33pF; C1206
C7, C8: 560pF; C1206
C9, C16: 1uF; C1206
C10, C11, C12, C13, C14: 0.1uF; C1206
D4: PESD1CAN; SPARKFUN-DISCRETESEMI_SOT23-3
DEBUG: LED3MM
E-STOP: PINHD-1X2; 1X02
IC1_2515: MCP2515; DIP18
IC2_2551: MCP2551DIL08; IC-PACKAGE_DIL08
IC3_4802: MCP4802; DIL08
LS1: BUZZER-PTH; BUZZER-12MM
POWER_OK: LED3MM
Q1: 16MHz; XTAL_ECS-160-20-46X
R2, R12, R13: 1K; R1206
R7, R8: 100; R1206
R9, R17: 4.7K; R1206
R11: 0; R1206
R14: 20K; R1206
R15, R16: 10k; R1206
RESET: MOMENTARY-SWITCH-SPST-PTH-6.0MM; TACTILE_SWITCH_PTH_6.0MM
X4: CLICK; ODO_JACK

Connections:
5V: C10.1, C11.1, C12.1, C13.1, E-STOP.1, IC1_2515.18 (VDD), IC2_2551.3 (VDD), IC3_4802.1, POWER_OK.A, R14.1, R17.1; also elsewhere on the board
BUZZER: LS1.+ (1); also elsewhere on the board
CANH: D4.1, IC2_2551.7 (CANH), R7.2; also elsewhere on the board
CANL: D4.2, IC2_2551.6 (CANL), R8.2; also elsewhere on the board
CAN_INT: IC1_2515.12 (INT); also elsewhere on the board
CAN_RXD: IC1_2515.2 (RXCAN), IC2_2551.4 (RXD)
CAN_SS: IC1_2515.16 (CS); also elsewhere on the board
CAN_TXD: IC1_2515.1 (TXCAN), IC2_2551.1 (TXD)
DACA: IC3_4802.8; also elsewhere on the board
DACB: IC3_4802.6; also elsewhere on the board
DAC_SS: IC3_4802.2; also elsewhere on the board
DEBUG_LED: DEBUG.A; also elsewhere on the board
ESTOP_INT: C16.1, R15.1; also elsewhere on the board
GND: C5.2, C6.2, C7.2, C8.2, C9.2, C10.2, C11.2, C12.2, C13.2, C14.2, C16.2, D4.3, IC1_2515.4 (TX0RTS), IC1_2515.5 (TX1RTS), IC1_2515.6 (TX2RTS), IC1_2515.9 (VSS), IC2_2551.2 (VSS), IC3_4802.5, IC3_4802.7, LS1.- (2), R2.1, R9.2, R12.1, R16.2, RESET.1, X4.P$2 (2), X4.P$3 (3); also elsewhere on the board
MISO: IC1_2515.15 (SO); also elsewhere on the board
MOSI: IC1_2515.14 (SI), IC3_4802.4; also elsewhere on the board
unnamed: R11.2, RESET.3 (2)
unnamed: C14.1, R13.2, R14.2
unnamed: DEBUG.K (C), R2.2
unnamed: E-STOP.2, R15.2, R16.1
unnamed: C7.1, R8.1
unnamed: C8.1, R7.1
unnamed: POWER_OK.K (C), R12.2
unnamed: IC2_2551.8 (RS), R9.1
OSC1: C6.1, IC1_2515.8 (OSC1), Q1.2
OSC2: C5.1, IC1_2515.7 (OSC2), Q1.1
RESET: R11.1; also elsewhere on the board
RS: IC1_2515.17 (RESET), R13.1
SCK: IC1_2515.13 (SCK), IC3_4802.3; also elsewhere on the board
WHEELROTATION: C9.1, R17.2, X4.P$1 (1); also elsewhere on the board

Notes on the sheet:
~Latch

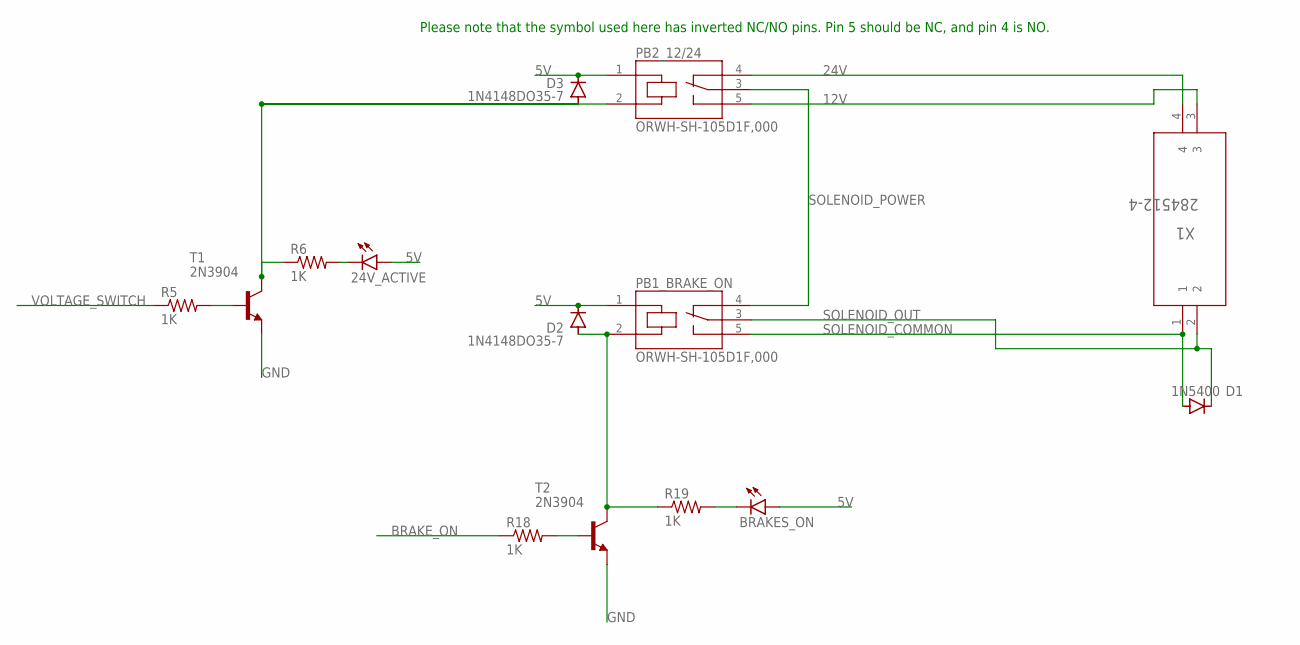
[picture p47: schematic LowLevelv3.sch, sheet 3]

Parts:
24V_ACTIVE: LED3MM
BRAKES_ON: LED3MM
D1: 1N5400; DO201-15
D2, D3: 1N4148DO35-7; DO35-7
PB1_BRAKE_ON, PB2_12/24: ORWH-SH-105D1F,000; TE_ORWH-SH-105D1F,000
R5, R6, R18, R19: 1K; R1206
T1, T2: 2N3904; TO92
X1: 284512-4

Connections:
5V: 24V_ACTIVE.A, BRAKES_ON.A, D2.C, D3.C, PB1_BRAKE_ON.1 (C1), PB2_12/24.1 (C1); also elsewhere on the board
12V: PB2_12/24.5 (NO), X1.3
24V: PB2_12/24.4 (NC), X1.4
BRAKE_ON: R18.1; also elsewhere on the board
GND: T1.3 (E), T2.3 (E); also elsewhere on the board
unnamed: R5.2, T1.2 (B)
unnamed: D3.A, PB2_12/24.2 (C2), R6.1, T1.1 (C)
unnamed: 24V_ACTIVE.K (C), R6.2
unnamed: R18.2, T2.2 (B)
unnamed: D2.A, PB1_BRAKE_ON.2 (C2), R19.1, T2.1 (C)
unnamed: BRAKES_ON.K (C), R19.2
SOLENOID_COMMON: D1.A, PB1_BRAKE_ON.5 (NO), X1.1
SOLENOID_OUT: D1.C, PB1_BRAKE_ON.3 (C), X1.2
SOLENOID_POWER: PB1_BRAKE_ON.4 (NC), PB2_12/24.3 (C)
VOLTAGE_SWITCH: R5.1; also elsewhere on the board

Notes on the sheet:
Please note that the symbol used here has inverted NC/NO pins. Pin 5 should be NC, and pin 4 is NO.

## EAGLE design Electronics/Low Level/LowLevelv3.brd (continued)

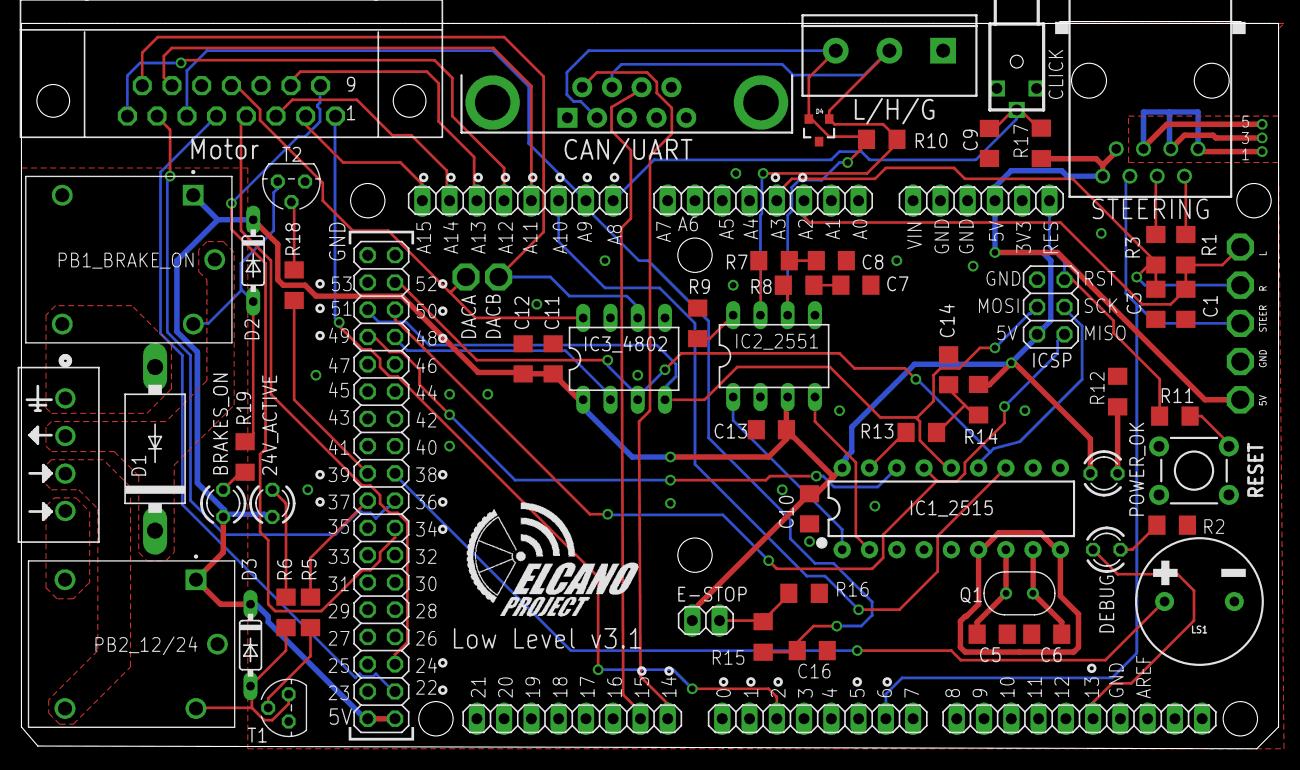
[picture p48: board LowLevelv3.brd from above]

Board: 2 copper layers, 117.1 x 67.6 mm, 71 parts (0 on the bottom side), 60 nets.

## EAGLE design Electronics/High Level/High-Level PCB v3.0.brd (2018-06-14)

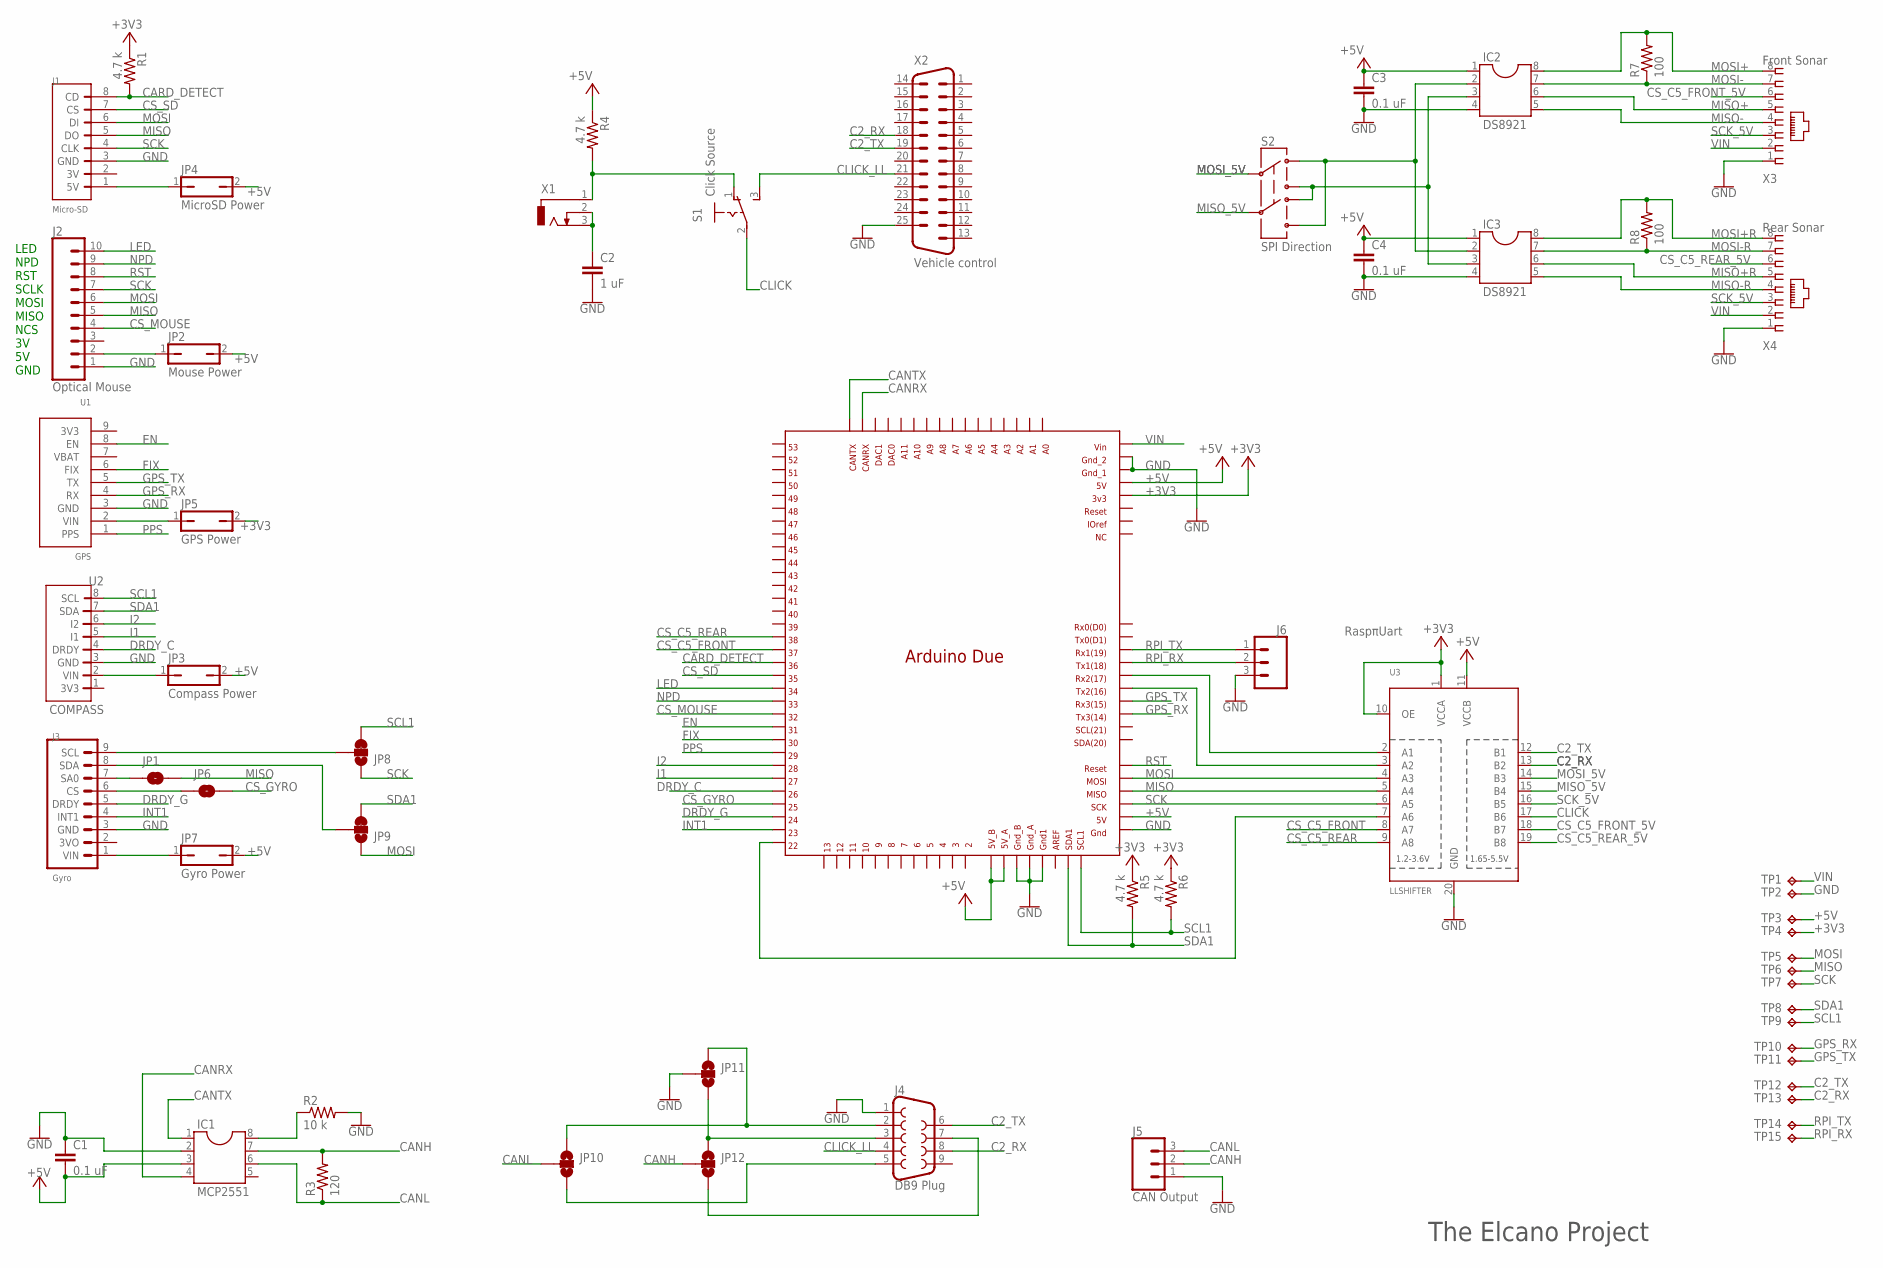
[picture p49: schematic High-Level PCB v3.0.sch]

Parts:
C1, C3, C4: 0.1 uF; C2.5-5
C2: 1 uF; C2.5-5
IC1: MCP2551; DIL08
IC2, IC3: DS8921; DIL08
J1: Micro-SD; ELSDCARD
J2: Optical Mouse; 1X10
J3: Gyro; ELGYRO
J4: DB9 Plug; DB9_MALE
J5: CAN Output; SCREWTERMINAL-5MM-3
J6: RaspπUart; 1X03
JP1, JP6: JUMPER-SMT_2_NO_SILK; SMT-JUMPER_2_NO_SILK
JP2: Mouse Power; JP1
JP3: Compass Power; JP1
JP4: MicroSD Power; JP1
JP5: GPS Power; JP1
JP7: Gyro Power; JP1
JP8, JP9: JUMPER-SMT_3_1-NC_TRACE_SILK; SMT-JUMPER_3_1-NC_TRACE_SILK
JP10, JP11, JP12: JUMPER-SMT_3_NO_SILK; SMT-JUMPER_3_NO_SILK
MCU1: DUE(NORMAL)
R1, R4, R5, R6: 4.7 k; 0204/7
R2: 10 k; 0204/7
R3: 120; 0204/7
R7, R8: 100; 0204/7
S1: Click Source; SP_ELSWITCH
S2: SPI Direction; DPDT
TP1, TP2, TP3, TP4, TP5, TP6, TP7, TP8, TP9, TP10, TP11, TP12, TP13, TP14, TP15: TPPAD1-17; P1-17
U1: GPS; ELGPS
U2: COMPASS; ELCOMPASS
U3: LLSHIFTER; ELSHIFTER
X1: 2.5MMJACK
X2: Vehicle control; M25H
X3: Front Sonar; RJ45-NO-SHIELD
X4: Rear Sonar; RJ45-NO-SHIELD

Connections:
+3V3: JP5.2, MCU1.3V3, R1.1, R5.1, R6.1, TP4.TP, U3.1 (VCCA), U3.10 (OE)
+5V: C1.2, C3.1, C4.1, IC1.3, IC2.1, IC3.1, JP2.2, JP3.2, JP4.2, JP7.2, MCU1.5V, MCU1.5V_A, MCU1.5V_B, MCU1.GND_ICSP, R4.1, TP3.TP, U3.11 (VCCB)
C2_RX: J4.8, TP13.TP, U3.13 (B2), X2.18
C2_TX: J4.6, TP12.TP, U3.12 (B1), X2.19
CANH: IC1.7, J5.2, JP12.2, R3.2
CANL: IC1.6, J5.3, JP10.2, R3.1
CANRX: IC1.4, MCU1.CANRX
CANTX: IC1.1, MCU1.CANTX
CARD_DETECT: J1.8 (CD), MCU1.36, R1.2
CLICK: S1.2, U3.17 (B6)
CLICK_LL: J4.4, S1.3 (S), X2.21
CS_C5_FRONT: MCU1.37, U3.8 (A7)
CS_C5_FRONT_5V: U3.18 (B7), X3.6
CS_C5_REAR: MCU1.38, U3.9 (A8)
CS_C5_REAR_5V: U3.19 (B8), X4.6
CS_GYRO: JP6.2, MCU1.25
CS_MOUSE: J2.4, MCU1.32
CS_SD: J1.7 (CS), MCU1.35
DRDY_C: MCU1.26, U2.4 (DRDY)
DRDY_G: J3.5 (DRDY), MCU1.24
EN: MCU1.31, U1.8 (EN)
FIX: MCU1.30, U1.6 (FIX)
GND: C1.1, C2.2, C3.2, C4.2, IC1.2, IC2.4, IC3.4, J1.3 (GND), J2.1, J3.3 (GND), J4.1, J5.1, J6.3, JP11.2, MCU1.5V_ICSP, MCU1.GND1, MCU1.GND_1, MCU1.GND_2, MCU1.GND_A, MCU1.GND_B, R2.2, TP2.TP, U1.3 (GND), U2.3 (GND), U3.20 (GND), X2.25, X3.1, X4.1
GPS_RX: MCU1.TX3, TP10.TP, U1.4 (RX)
GPS_TX: MCU1.RX3, TP11.TP, U1.5 (TX)
I1: MCU1.27, U2.5 (I1)
I2: MCU1.28, U2.6 (I2)
INT1: J3.4 (INT1), MCU1.23
LED: J2.10, MCU1.34
MISO: J1.5 (DO), J2.5, JP1.2, MCU1.MISO_ICSP, TP6.TP, U3.5 (A4)
MISO+: IC2.6, X3.5
MISO+R: IC3.6, X4.5
MISO-: IC2.5, X3.4
MISO-R: IC3.5, X4.4
MISO_5V: S2.5, U3.15 (B4)
MOSI: J1.6 (DI), J2.6, JP9.1, MCU1.MOSI_ICSP, TP5.TP, U3.4 (A3)
MOSI+: IC2.8, R7.2, X3.8
MOSI+R: IC3.8, R8.2, X4.8
MOSI-: IC2.7, R7.1, X3.7
MOSI-R: IC3.7, R8.1, X4.7
MOSI_5V: S2.2, U3.14 (B3)
unnamed: C2.1, X1.2, X1.3
unnamed: IC2.2, IC3.2, S2.1, S2.6
unnamed: IC2.3, IC3.3, S2.3, S2.4
unnamed: MCU1.TX2, U3.3 (A2)
unnamed: MCU1.RX2, U3.2 (A1)
unnamed: R4.2, S1.1 (O), X1.1
unnamed: JP3.1, U2.2 (VIN)
unnamed: J3.1 (VIN), JP7.1
unnamed: J1.1 (5V), JP4.1
unnamed: J4.3, JP11.3, JP12.1
unnamed: MCU1.22, U3.7 (A6)
unnamed: J2.2, JP2.1
unnamed: JP5.1, U1.2 (VIN)
unnamed: J4.5, JP10.3
unnamed: J4.7, JP12.3
unnamed: IC1.8, R2.1
unnamed: J4.2, JP10.1, JP11.1
unnamed: J3.6 (CS), JP6.1
unnamed: J3.7 (SA0), JP1.1
unnamed: J3.8 (SDA), JP9.2
unnamed: J3.9 (SCL), JP8.2
NPD: J2.9, MCU1.33
PPS: MCU1.29, U1.1 (PPS)
RPI_RX: J6.2 (1), MCU1.TX1, TP15.TP
RPI_TX: J6.1 (2), MCU1.RX1, TP14.TP
RST: J2.8, MCU1.RESET_ICSP
SCK: J1.4 (CLK), J2.7, JP8.1, MCU1.SCK_ICSP, TP7.TP, U3.6 (A5)
SCK_5V: U3.16 (B5), X3.3, X4.3
SCL1: JP8.3, MCU1.SCL1, R6.2, TP9.TP, U2.8 (SCL)
SDA1: JP9.3, MCU1.SDA1, R5.2, TP8.TP, U2.7 (SDA)
VIN: MCU1.VIN, TP1.TP, X3.2, X4.2

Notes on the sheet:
LED NPD RST SCLK MOSI MISO NCS 3V 5V GND
The Elcano Project

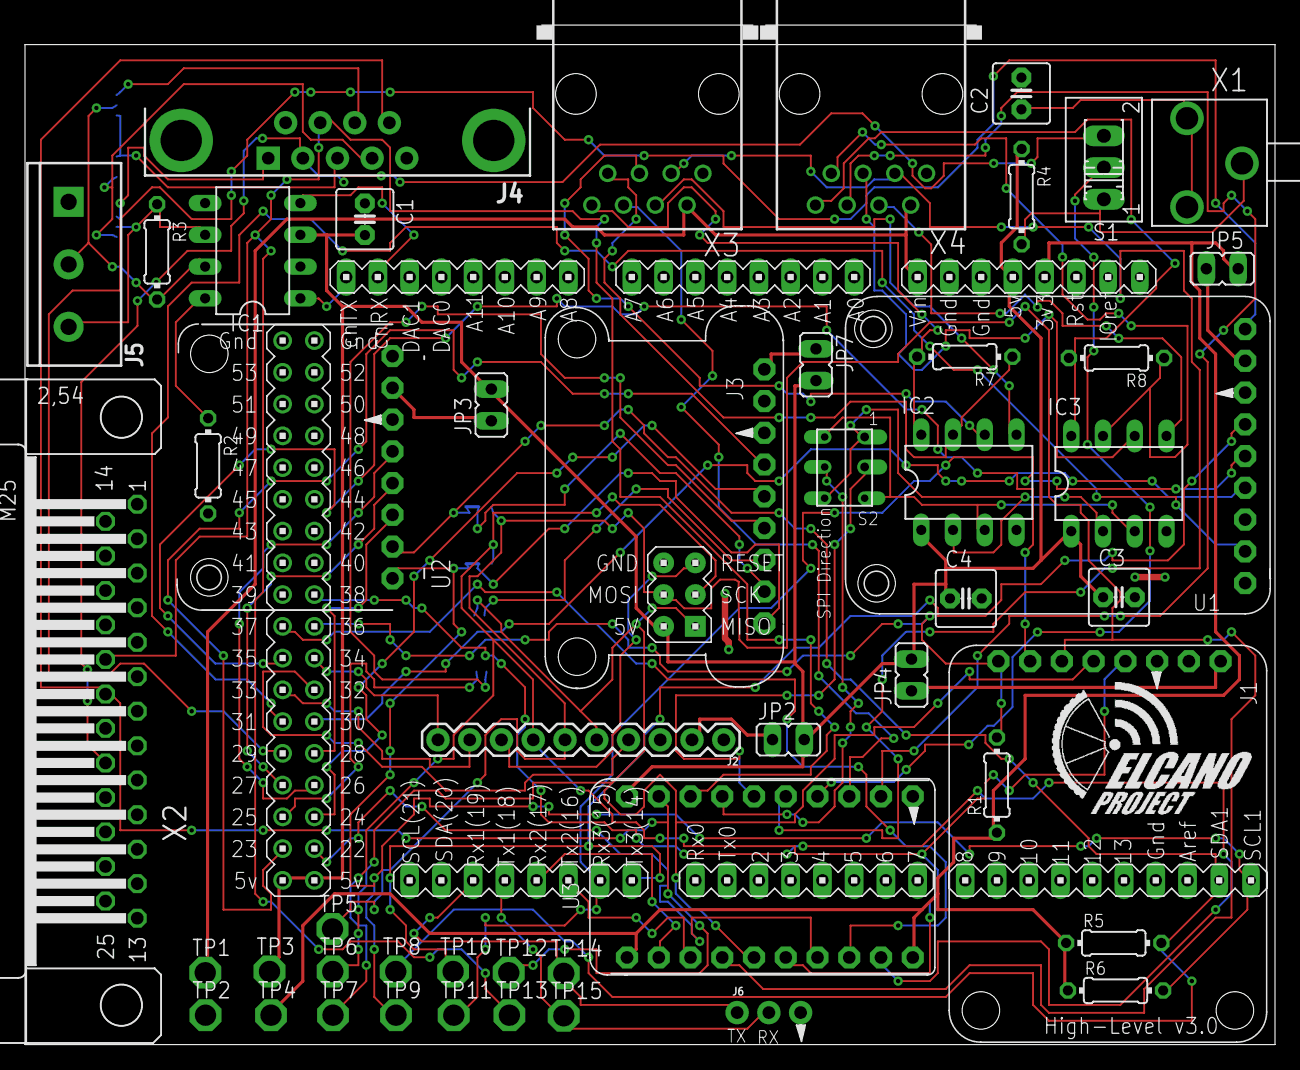
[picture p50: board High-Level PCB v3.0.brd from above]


Board: 2 copper layers, 100.0 x 81.6 mm, 58 parts (7 on the bottom side), 72 nets.

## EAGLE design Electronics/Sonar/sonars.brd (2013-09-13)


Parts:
F-RNG: Front; 1X07
FL-RNG: Front left; 1X07
FR-RNG: Front right; 1X07
L-RNG: Left; 1X07
L-RNG1: Back Left; 1X07
R-RNG: Right; 1X07
R-RNG1: Back Right; 1X07
X1: RJ45-8L-B; RJ45-NO-SHIELD

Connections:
+5V: F-RNG.6, FL-RNG.6, FR-RNG.6, L-RNG.6, L-RNG1.6, R-RNG.6, R-RNG1.6, X1.1
CHN: F-RNG.4, X1.2
F>FL: F-RNG.5, FL-RNG.4
FL>FR: FL-RNG.5, FR-RNG.4
FL_RNG: FL-RNG.3, X1.5
FR>R: FR-RNG.5, R-RNG.4, R-RNG1.4
FR_RNG: FR-RNG.3, X1.6
F_RNG: F-RNG.3, X1.4
GND: F-RNG.1, F-RNG.7, FL-RNG.1, FL-RNG.7, FR-RNG.1, FR-RNG.7, L-RNG.1, L-RNG.7, L-RNG1.1, L-RNG1.7, R-RNG.1, R-RNG.7, R-RNG1.1, R-RNG1.7, X1.3
L_RNG: L-RNG.3, L-RNG1.3, X1.7
R>L: L-RNG.4, L-RNG1.4, R-RNG.5, R-RNG1.5
R_RNG: R-RNG.3, R-RNG1.3, X1.8

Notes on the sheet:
Select chaining
Range PW
Range Analog
Vcc
Gnd


Board: 2 copper layers, 91.4 x 64.8 mm, 8 parts (0 on the bottom side), 12 nets.

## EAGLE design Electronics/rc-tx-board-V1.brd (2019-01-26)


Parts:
9.6VDC: DCJ0202
A-NC1, A-NC2: PINHD-1X2; 1X02
ANGLE: LED5MM
ANLG: PINHD-1X17; 1X17
AUTO: LED5MM
AUTO-SW: TL36PO; TL3XPO
C1, C2: 100nF; C050-024X044
D9: LED5MM
DIG: PINHD-1X17; 1X17
ESTP: LED5MM
ESTP-SW: TL36PO; TL3XPO
GNDA: PINHD-1X2; 1X02
GNDT: PINHD-1X2; 1X02
LR+: PINHD-1X2; 1X02
PWR: LED5MM
PWR-SW: TL36PO; TL3XPO
R1, R3, R4, R5, R6, R7, R9: 1k; 0207/10
R2: 22k; 0207/10
R8: 10k; 0207/10
RADIO: PINHD-1X3; 1X03
T-NC1, T-NC2: PINHD-1X2; 1X02
THRT: LED5MM
TX: LED5MM
UD+T: PINHD-1X2; 1X02

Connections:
5V: ANLG.6, LR+.1, PWR.A, UD+T.1
9.6V: ANLG.3, C1.1, C2.1, PWR-SW.3 (S), R2.2, RADIO.1
9.6V_SOURCE: 9.6VDC.1, PWR-SW.2
ANGLE: ANGLE.A, DIG.8
ANGLE_R: ANGLE.K (C), R1.2
ANGLE_SENS: ANLG.13, LR+.2
AUTO: AUTO.A, DIG.12
AUTO_R: AUTO.K (C), R5.2
AUTO_SW: ANLG.11, AUTO-SW.2
BAT_HEALTH: ANLG.10, R2.1, R8.2
ESTP: DIG.13, ESTP.A
ESTP_R: ESTP.K (C), R6.2
ESTP_SW: ANLG.12, ESTP-SW.2
GND: 9.6VDC.3, ANLG.5, AUTO-SW.3 (S), C1.2, C2.2, DIG.6, ESTP-SW.3 (S), GNDA.2, GNDT.2, R1.1, R3.1, R4.1, R5.1, R6.1, R7.1, R8.1, R9.1, RADIO.3
PWR_R: PWR.K (C), R4.2
RADIO_SIG: DIG.17, RADIO.2
SPARE: D9.A, DIG.14
SPARE_R: D9.K (C), R7.2
THROTTLE_SENS: ANLG.14, GNDT.1
THRT: DIG.10, THRT.A
THRT_R: R3.2, THRT.K (C)
TX: DIG.16, TX.A
TX_R: R9.2, TX.K (C)

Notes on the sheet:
These must be matched to the right pins on the joystick.
Angle
Throttle


Board: 2 copper layers, 100.0 x 80.0 mm, 33 parts (0 on the bottom side), 23 nets.

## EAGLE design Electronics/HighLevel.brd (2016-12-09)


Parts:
C1: 1 uF; C025-030X050
C3L: Pilot digital; 1X17
C3R: Pilot analog; 1X17
C5, C6: 0.1uF; C2.5-2
C6A0-7: C6 Analog In 0-7; 1X08
C6D0-7, C6D14-21: GPS; 1X08
C6D8-13: C6D8-13; 1X10
D22-53: High digital; 2X18
DAC: MCP 4802; DIL08
IC2, IC3: DS 8291; DIL08
ICSP: C6; 2X03
JP1: 5V_JP1; JP1
JP2: 3V3_JP2; JP1
JP3: 5V_JP3; JP1
JP4: 3V3_JP4; JP1
JP5: C4 Mapper; 1X09
POWER: C6 Power; 1X08
R1: 4.7 K; 0207/10
R3, R4: 100; 0204/5
X1, X4: RJ45-8L-B; RJ45-NO-SHIELD
X2: Vehicle control; M25H
X3: 2odo__; ODO_JACK
X5: Compass; 1X08
X7: Mouse; 1X10
X8: Digital Compass; 1X08

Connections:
2TX6RX: C3L.17, C6D14-21.4, JP5.6, X2.19
3MISO: C3R.2, IC2.3, IC3.3
3MOSI: C3L.1, DAC.4, IC2.2, IC3.2
3SCK: C3R.1, DAC.3, X1.3, X4.3
3SCL: C3L.8, JP5.9
3SDA: C3L.7, JP5.8
3SS5R: C3L.13, X4.6
3SS_DAC: C3L.14, DAC.2
3TX2RX: C3L.3, X2.18
3V3: JP2.1, JP4.1, POWER.5
3VLSM: JP2.2, X5.8, X8.8
5VLSM: JP1.2, X5.7, X8.7
5V_C3: C3R.6, DAC.1
6MISO: C6D8-13.6, D22-53.31, ICSP.1, X7.5
6MOSI: C6D8-13.7, D22-53.32, ICSP.4, X7.6
6SCL: C6D8-13.1, C6D14-21.8, X5.1, X8.1
6SDA: C6D8-13.2, C6D14-21.7, X5.2, X8.2
6TX2RX: C6D14-21.5, X2.20
+5V: C5.1, C6.1, IC2.1, IC3.1, ICSP.2, JP1.1, JP3.1, POWER.4, POWER.7, R1.2
A0: C3R.14, C6A0-7.1
A1: C3R.13, C6A0-7.2
A5: C3R.9, C6A0-7.6
ACK26: C6D0-7.4, X2.17
ACK34: C3L.15, JP5.5, X2.9
ACK43: C3L.16, JP5.4
ACK62: C6D0-7.3, X2.22
AUTREQ: C3L.9, C6D0-7.5, X2.7
CLICK: C6D0-7.6, R1.1, X2.21, X3.P$1 (1)
CRSSTR: DAC.6, X2.6
CRSTHR: DAC.8, X2.8
CRS_RVS: C3L.10, X2.13
D09: D22-53.18, X2.14
DRDY: D22-53.7, X5.5, X8.5
GND: C1.1, C3R.4, C5.2, C6.2, D22-53.36, DAC.5, DAC.7, IC2.4, IC3.4, ICSP.6, POWER.2, POWER.3, X1.1, X2.25, X4.1, X5.6, X7.1, X8.6
I1LSM: D22-53.11, X5.4, X8.4
I2LSM: D22-53.9, X5.3, X8.3
LED1: C6D8-13.10, X2.5
LED3: C3R.17, X2.4
LED4: D22-53.34, JP5.7, X2.3
LED5: D22-53.30, X2.2, X7.10
LED6: D22-53.17, X2.1
LED7: D22-53.14, X2.15
LED8: D22-53.12, X2.16
M3V: JP4.2, X7.3
M5V: JP3.2, X7.2
MANRQ: C3L.11, X2.10
MISO+: IC2.6, X1.5
MISO+R: IC3.6, X4.5
MISO-: IC2.5, X1.4
MISO-R: IC3.5, X4.4
MOSI+: IC2.8, R3.1, X1.8
MOSI+R: IC3.8, R4.1, X4.8
MOSI-: IC2.7, R3.2, X1.7
MOSI-R: IC3.7, R4.2, X4.7
unnamed: C3L.2, X1.6
unnamed: C1.2, X3.P$2 (2), X3.P$3 (3)
NAV_FIX: C6D14-21.3, JP5.3
NCS: D22-53.27, X7.4
NPO: D22-53.29, X7.9
PATH: C3L.4, JP5.2
RDY26: D22-53.16, X2.12
RDY32: C3L.12, X2.11
RDY62: C6D0-7.2, X2.23
RESET: C3L.5, C3R.5, ICSP.5, JP5.1, POWER.6, X7.8
SCLK: C6D8-13.5, D22-53.33, ICSP.3, X7.7
VIN: C3R.3, POWER.1, X1.2, X4.2

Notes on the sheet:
pwm
Gnd
D10
D11
D12
D13
D09
D08
VIN
Rx D0
Tx D1
Reset
Ground
D14 Tx3
D15 Rx3
D16 Tx2
D17 Rx2
D18 Tx1
D19 Rx1
D20 Int4
D21 Int5
MISO
MOSI
SCLK
SCK
Vcc
GND
D52
D22
RST
C3_SS
3.3V
AREF
DRDY
GPS
Vision
D27
D29
D31
D25



Board: 2 copper layers, 99.8 x 80.0 mm, 30 parts (4 on the bottom side), 66 nets.

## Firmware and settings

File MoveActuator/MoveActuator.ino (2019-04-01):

<<<<<<< HEAD
/********************************************************************************
 Move Actuator: Reduced version of Elcano_C2_Base for testing actuators
 
 Elcano Control Module C2 Basic: Bare bones low level control of vehicle.
 
 Outputs are
 1) Analog 0-4 V signal for traction motor speed
 2) Four relay signals for brakes.
 3) PWM signal for steering.
 ********************************************************************************/

// Input/Output (IO) pin names for the MegaShieldDB printed circuit board (PCB)
 #include "IOPCB.h"
// Contains trike definitions 
 #include "Settings.h"
// When setting up the project, select
//   Sketch  |  Import Library ... |  SPI
// include the Serial Periferal Interface (SPI) library:
#include <SPI.h>
=======
/*
  Move Actuator: Reduced version of Elcano_C2_Base for testing actuators

  Elcano Contol Module C2 Basic: Bare bones low level control of vehicle.

  Outputs are
  1) Analog 0-4 V signal for traction motor speed
  2) Four relay signals for brakes.
  3) PWM signal for steering.
*/

#include <SPI.h>
#include <Servo.h>

/*==========================================================================*/
// @ToDo: Provide a means to select the model of trike rather than hard-coded values
/*==========================================================================*/


#define BRAKE_POWER 9
#define BRAKE_VOLTAGE 10
>>>>>>> moveactuator updated to work with known values for Servo.h and the yellow trike

/********************************************************************************
@ToDo: Fix this fix. If there are variant systems, they should be selected
in Settings.h, and then IO.h can be included *after* that, and test the
selector, or use values defined in Settings.h.
Temporary fix 10/7/15:   IOPCB.h is here
Possibly fixed: 10/8/18
IOCPB.h section has been commented out and code compiles with the include 
Settings.h section has also been commented out and code compiles with the include 
*********************************************************************************/

/********************************************************************************
// Values (0-255) represent digital values that are PWM signals used by analogWrite.
// MIN and MAX ACC set the minimum signal to get the motor going, and maximum allowable acceleration for the motor
#define MIN_ACC_OUT 50
#define MAX_ACC_OUT 235

<<<<<<< HEAD
// RIGHT, STRAIGHT, and LEFT TURN_OUT set values to be sent to the steer actuator that changes the direction of the front wheels
#define RIGHT_TURN_OUT 229
#define LEFT_TURN_OUT 127
#define STRAIGHT_TURN_OUT 178

// RIGHT, STRAIGHT, and LEFT TURN_MS are pulse widths in msec received from the RC controller
#define RIGHT_TURN_MS 1000
#define LEFT_TURN_MS 2000
#define STRAIGHT_TURN_MS 1500
=======
/*
 * STEERING
 * RIGHT, STRAIGHT, and LEFT TURN_OUT set values to be sent to the steer actuator that changes the direction of the front wheels
 * 
 * 1000 uS maps to Servo.h using a value of 142
 * 2000 uS maps to Servo.h using a value of 45
 * 
 * The yellow trike has a mechanical range of (70-140) and a center at approximately 90
 */
#define RIGHT_TURN_OUT 140
#define LEFT_TURN_OUT 70
#define STRAIGHT_TURN_OUT 94
#define STEER_OUT_PIN 8 // Output to steer actuator on this digital pin
>>>>>>> moveactuator updated to work with known values for Servo.h and the yellow trike

// Turn sensors are believed if they are in this range while wheels are straight
// These numbers vary considerably, depending on which sensor angle is set to straight.
#define RIGHT_MIN_COUNT 80
#define RIGHT_MAX_COUNT 284
#define LEFT_MIN_COUNT  80
#define LEFT_MAX_COUNT  284

// Trike specific pins/channels
// Output to motor actuator
#define DAC_CHANNEL 0
<<<<<<< HEAD
// Output to steer actuator
#define STEER_OUT_PIN 7
// Output to brake actuator
//#define BRAKE_OUT_PIN 6
// DISK_BRAKE is deprecated, use BRAKE_OUT_PIN
=======
>>>>>>> moveactuator updated to work with known values for Servo.h and the yellow trike

// Trike-specific physical parameters
#define WHEEL_DIAMETER_MM 482
// Wheel Circumference
#define WHEEL_CIRCUM_MM (long) (WHEEL_DIAMETER_MM * PI)
//    Turning radius in cm.
#define TURN_RADIUS_CM 209
//    Turning speed in degrees per ms.
#define TURN_SPEED_DPMS 29700
//    Smallest change in turning angle, in millidegrees
#define TURN_RESOLUTION_MDEG 60
//    Maximum turning angle, in degrees
#define TURN_MAX_DEG 30
//  Motor
#define MOTOR_POLE_PAIRS 23
// maximum allowed speed
#define MAX_SPEED_KPH 15

// Use DAC A
#define THROTTLE_CHANNEL 0

// ====== End Settings.h ======================
********************************************************************************/


// Define the tests to do.
#define BRAKE_RAMP
#define STEER_RAMP
#define MOTOR_RAMP
// If operating with the MegaShieldDB, we can use the Digital Analog Converter to move the vehicle
#define DAC

/*
The Mega is designed to be used with a data-logging shield.
The nonMega shield uses A4 and A5 for RTC and D10,11,12,and 13 for MOSI data logging.
*/
/********************************************************************************
// @ToDo: There are declarations here that are per-trike, and some that are common.
// Parameters have been added to Settings.h for the per-trike values.
// Should the common parameters also be defined in Settings.h?

// DIGITAL I/O ----------------------------------------------

// D0-7 Connector -------------------------------
// On the Mega, any of D0 to D13 can be PWM.
// D0 is (Rx0) Read Serial Data. 
const int Rx0 = 0;      // external input
// [out] Digital Signal 1: (Tx0). Transmit Serial Data.  
const int Tx0 = 1;      // external output

// This is the 5V supply produced by the E-bike controller.
//  If it goes away, 36V power has been turned off (presumably by the rider's key switch).
//const int EStop =   2;         // external input
const int WheelClick = 2;      //  was 3; interrupt; Reed switch generates one pulse per rotation.

// D8-13 Connector ----------------------
// The shield does not provide a socket for D8-13
// D8 is spare on X4-2;  D9 is spare on X5-2.
// Signals D10-13 are not brought out on connectors, and may be used by a shield.
const int SDchipSelect = 10;  // for some shields
const int LED = 13;

// D14 - 21 Connector -------------------------------------
const int RxD2 = 14;      // reserved external input on X2-19
// Message in Gamebots format giving wheel spin rate and steering angle.
const int TxD2 = 15;      // Cruise Drive Command
const int RxD3 = 16;      // available on X2-22
const int TxD3 = 17;      // available on X2-20
/*  
The Stop signal is a momentary button push from either the console or remote.
A rising edge produces an interrupt.
The Cruise button works the same way.
The ~Estop signal is the 5V supply produced by the motor controller.
This supply goes away when either the key switch is turned off or RC4 is pressed.
Lack of 5V from the motor controller is an emergency stop.
Interrupts are on 2,3,18,19,20 and 21.
*/
/********************************************************************************
const int SelectCD     = 49;  // Select IC 3 DAC (channels C and D)
const int ThrottleMISO = 50;
const int ThrottleMOSI = 51;
const int ThrottleSCK  = 52;
const int SelectAB     = 53;  // Select IC 2 DAC (channels A and B)

//==========================================================================
// End of IOPCB.h
//==========================================================================
********************************************************************************/

// The MegaShieldDB has a four channel Digital to Analog Converter (DAC).
// Basic Arduino cannot write a true analog signal, but only PWM.
// Many servos take PWM.
// An electric bicycle (E-bike) throttle expects an analog signal.
// We have found that feeding a pwm signal to an e-bike controller makes the motor chug at low speed.

#ifndef TRUE
#define TRUE 1
#define FALSE 0
#endif


// Values to send over DAC
const int FullThrottle =  MAX_ACC_OUT;   // 3.63 V
const int MinimumThrottle = MIN_ACC_OUT;  // Throttle has no effect until 1.2 V
// Values to send on PWM to get response of actuators
// Steering
const int HardLeft = LEFT_TURN_OUT;
const int Straight = STRAIGHT_TURN_OUT;
const int HardRight = RIGHT_TURN_OUT;

// set the initial positions
int ThrottlePosition = MinimumThrottle;
int SteerPosition = Straight;

int SteerIncrement = 1;
int ThrottleIncrement = 1;


/*  Elcano #1 Servo range is 100 mm for steering.

    Elcano servo has a hardware controller that moves to a
    particular position based on an input PWM signal from Arduino.
    The Arduino PWM signal is a square wave at a base frequency of 490 Hz or 2.04 ms.
    PWM changes the duty cycle to encode   
    0 is always off; 255 always on. One step is 7.92 us.
    
    Elcano servo is fully retracted on a pulse width of 2 ms;
    fully extended at 1 ms and centered at 1.5 ms.
    There is a deadband of 8 us.
    At 12v, servo operating speed is 56mm/s with no load or
    35 mm/s at maximum load.
    
    Output from hardware servo controller to either servo has five wires, with observed bahavior of:
    White: 0V
    Yellow: 5V
    Blue: 0-5V depending on position of servo.
    Black: 12V while servo extends; 0V at rest or retracting.
    Red:   12V while retracting; 0V at rest or extending.
    The reading on the Blue line has hysteresis when Elcano sends a PWM signal; 
    there appear to be different (PWM, position) pairs when retracting or extending.
    Motor speed is probably controlled by the current on the red or black line.   
*/
/*---------------------------------------------------------------------------------------*/ 

/* Solenoid controlled Brakes.
 *  
 *  Solenoid (Johnson Electic model 150 174432-024) 
 *  can be kept at lower voltage (12V) indefinitely. 
 *  It has a holding force of 14.5 lb.
 *  At the higher voltage, data sheet expects it to be high (24V) for
 *  25% of the time and low for 75%. However, it can stay high for 100 sec.
 *  The solenoid typically reacts in less than a second.
 *  For 0.25 inch throw and 24V it can pull 7 lb.
 *  We are using the part with 0.3 inch throw, 12V in low state and 36V in high
 *  state, but keeping voltage high for only a second or two.
 *  This appears to be within the part's capabilities.
 *  
 *  The solenoid brake on Elcano replaces the earlier linear actuator.
 *  Solenoid advantages:
 *      Faster: Typically 0.2 seconds vs 2 in/sec for no load. 
 *      Slightly Lighter: 482 grams each vs. 1.16 kg
 *      Available; Linear actuator is no longer available for 2 or 4 inch throw.
 *      Less expensive: 2 * $70 vs. $250
 *      More durable; 5 of the linear actutors have failed.
 *  Linear actuator advantages:
 *      Single unit can pull both brakes (25 lb. thrust); solenoid requires a unit for each brake.
 *      No restriction on throw length; solenoid will not work with > 0.3 inch throw.
 *      Maintains last position without power.   
 *      Do not need to worry about heat dissipation.
 *      
 *  The linear actuator was controlled by pulse width on one digital line.    
 *  The solenoids are controlled by relays on two digital lines.
 *      
 *    Tyler Folsom   April 2018  
 *    
     *  Expected behavior
     *  When Green LED is on, NO is connected to COM; NC is not
     *  Writing HIGH to a relay will turn LED on, and connect NO to COM
     *  When green LED is off, NC is connected to COM; NO is not.
     *  Writing LOW to a relay will turn LED off, and connect NC to COM.
     *  You shoud hear a click when the relay operates.
     *  If there is a change in LED, but no click, the relay does not have enough power.
     */
   
class Brakes
{
<<<<<<< HEAD
 public:
  Brakes();
  void Stop();
  void Release();
  void Check();
 private:
  enum brake_state {BR_OFF, BR_HI_VOLTS, BR_LO_VOLTS} state;
  unsigned long clock_hi_ms;
  const int LeftBrakeOnPin = 10;
  const int RightBrakeOnPin = 4;
  const int LeftBrakeVoltPin = 8;
  const int RightBrakeVoltPin = 7;
  const unsigned long MaxHi_ms = 800;
 } ;
=======
  public:
    Brakes();
    void Stop();
    void Release();
    void Check();
  private:
    enum brake_state {BR_OFF, BR_HI_VOLTS, BR_LO_VOLTS} state;
    unsigned long clock_hi_ms;
    const int brakePower = BRAKE_POWER; // LOW means on, HIGH means off
    const int brakeOn = BRAKE_VOLTAGE; // LOW means 24v, HIGH means 12v
    const unsigned long MaxHi_ms = 800;
} ;
>>>>>>> moveactuator updated to work with known values for Servo.h and the yellow trike

// For normal operation
const long int loop_time_ms = 100;  // Limits time in the loop.

 Brakes brake = Brakes();
 

/*---------------------------------------------------------------------------------------*/
void setup()
{
    //Set up pin modes and interrupts, call serial.begin and call initialize.
    Serial.begin(9600);
    
    // SPI: set the slaveSelectPin as an output:
    pinMode (SelectAB, OUTPUT);
    pinMode (SelectCD, OUTPUT);
    pinMode (10, OUTPUT);
    SPI.setDataMode( SPI_MODE0);
    SPI.setBitOrder( MSBFIRST);
    // initialize SPI:
    // The following line should not be neccessary. It uses a system library.
//    PRR0 &= ~4;  // turn off PRR0.PRSPI bit so power isn't off
    SPI.begin(); 
    for (int channel = 0; channel < 4; channel++)
        DAC_Write (channel, 0);   // reset did not clear previous states
 
    pinMode(STEER_OUT_PIN, OUTPUT);

    brake.Release();   // release brake
    moveSteer(SteerPosition);
    moveVehicle(MinimumThrottle); 
    Serial.println("Initialized");
    Serial.print("Left\t");   
    Serial.print("Right\t");
    Serial.println("Time");   
}
/*---------------------------------------------------------------------------------------*/
void loop()
{
  static int BrakeStep;
  // Apply actuators no faster than MinTimeStep_msec
  const unsigned long MinTimeStep_msec = 100;
  unsigned long delay_ms = 0;
  unsigned long timeStart_ms = millis();
// Put no new code before here
  
  // apply throttle
#ifdef MOTOR_RAMP
    ThrottlePosition += ThrottleIncrement;
    if (ThrottlePosition > FullThrottle || ThrottlePosition < MinimumThrottle)
        ThrottleIncrement = -ThrottleIncrement; 
    moveVehicle(ThrottlePosition);
#endif  // MOTOR_RAMP  
  
  // apply brakes
#ifdef BRAKE_RAMP
 if (BrakeStep == 1)
   brake.Stop();
 if (BrakeStep == 40)
   brake.Release();
 brake.Check();
 if (++BrakeStep > 80)
    BrakeStep = 0;
 
#endif  // BRAKE_RAMP  
  
 // apply steering
#ifdef STEER_RAMP
    SteerPosition += SteerIncrement;
    if (SteerPosition > HardRight || SteerPosition < HardLeft)
        SteerIncrement = -SteerIncrement;
    moveSteer(SteerPosition);
#endif  // Steer_RAMP
  outputToSerial();

// Put no new code after here.
  unsigned long execution_ms = millis() - timeStart_ms;
  delay_ms = MinTimeStep_msec - execution_ms;
  if (delay_ms > 0) delay(delay_ms);
}
/*---------------------------------------------------------------------------------------*/
void moveSteer(int i)
{
     Serial.print ("Steer "); Serial.print(i);
     Serial.print (" on ");   Serial.println (STEER_OUT_PIN);
     analogWrite(STEER_OUT_PIN, i);
}
/*---------------------------------------------------------------------------------------*/
void outputToSerial()
{
#ifdef MOTOR_RAMP
  //put output data for motor here
#endif  // MOTOR_RAMP  
  
#ifdef BRAKE_RAMP
  //put output data for brake here
#endif  // BRAKE_RAMP

#ifdef STEER_RAMP 
     int left = analogRead(A2);               //Steer
     int right = analogRead(A3);
     Serial.print(left);   Serial.print("\t"); //Left turn sensor
     Serial.print(right);  Serial.print("\t"); //Right turn sensor
#endif //STEER_RAMP
  Serial.println(micros()); //Current time and end line
}
/*---------------------------------------------------------------------------------------*/
void moveVehicle(int counts)
{
    /* Observed behavior on ElCano #1 E-bike no load (May 10, 2013, TCF)
      0.831 V at rest       52 counts
      1.20 V: nothing       75
      1.27 V: just starting 79
      1.40 V: slow, steady  87
      1.50 V: brisker       94
      3.63 V: max          227 counts     
      255 counts = 4.08 V      
      */
     Serial.print ("Motor "); Serial.print(counts);
     Serial.print (" on ");   Serial.println (THROTTLE_CHANNEL);
#ifdef DAC      
   DAC_Write(THROTTLE_CHANNEL, counts);
#endif
}
/*---------------------------------------------------------------------------------------*/
/* DAC_Write applies value to address, producing an analog voltage.
// address: 0 for chan A; 1 for chan B; 2 for chan C; 3 for chan D
// value: digital value converted to analog voltage
// Output goes to mcp 4802 Digital-Analog Converter Chip via SPI
// There is no input back from the chip.
*/
void DAC_Write(int address, int value)

/*
REGISTER 5-3: WRITE COMMAND REGISTER FOR MCP4802 (8-BIT DAC)
A/B  —  GA  SHDN  D7 D6 D5 D4 D3 D2 D1 D0 x x x x
bit 15                                       bit 0

bit 15   A/B: DACA or DACB Selection bit
         1 = Write to DACB
         0 = Write to DACA
bit 14   — Don’t Care
bit 13   GA: Output Gain Selection bit
         1 = 1x (VOUT = VREF * D/4096)
         0 = 2x (VOUT = 2 * VREF * D/4096), where internal VREF = 2.048V.
bit 12   SHDN: Output Shutdown Control bit
         1 = Active mode operation. VOUT is available. 
         0 = Shutdown the selected DAC channel. Analog output is not available at the channel that was shut down.
         VOUT pin is connected to 500 k (typical)
bit 11-0 D11:D0: DAC Input Data bits. Bit x is ignored.

With 4.95 V on Vcc, observed output for 255 is 4.08V.
This is as documented; with gain of 2, maximum output is 2 * Vref
*/

{
  int byte1 = ((value & 0xF0)>>4) | 0x10; // acitve mode, bits D7-D4
  int byte2 = (value & 0x0F)<<4;           // D3-D0
  if (address < 2)
  {
      // take the SS pin low to select the chip:
      digitalWrite(SelectAB,LOW);
      if (address >= 0)
      { 
        if (address == 1)
          byte1 |= 0x80;  // second channnel
        SPI.transfer(byte1);
        SPI.transfer(byte2);
       }
      // take the SS pin high to de-select the chip:
      digitalWrite(SelectAB,HIGH);
  }
  else
  {
      // take the SS pin low to select the chip:
      digitalWrite(SelectCD,LOW);
      if (address <= 3)
      {
        if (address == 3)
          byte1 |= 0x80;  // second channnel
        SPI.transfer(byte1);
        SPI.transfer(byte2);
      }
       // take the SS pin high to de-select the chip:
      digitalWrite(SelectCD,HIGH);
  }
}
 
Brakes::Brakes()
{
  pinMode( LeftBrakeOnPin, OUTPUT);
  pinMode( RightBrakeOnPin, OUTPUT);
  pinMode( LeftBrakeVoltPin, OUTPUT);
  pinMode( RightBrakeVoltPin, OUTPUT);
  clock_hi_ms = millis();
  state = BR_OFF;
}
void Brakes::Release()
{
  /*  Expected behavior:
   * LEDs go off for relays 2 and 3;
   * Relay 2 has NO (connected to solenoids) open, and there is no power to solenoids.
   * Relay 3 connects COM (other end of solenoid) to NO (12V) 
   */
  digitalWrite(LeftBrakeOnPin, LOW);
  digitalWrite(LeftBrakeVoltPin, LOW);
  digitalWrite(RightBrakeOnPin, LOW);
  digitalWrite(RightBrakeVoltPin, LOW);
  state = BR_OFF;
}
void Brakes::Stop()
{
  /*  Expected behavior:
   *  Both LEDs come on for Relays 2 and 3
   *  Relay 2 connects NO (solenoids) to COM (ground)
   *  Relay 3 connects COM (other end of solenoids) to NC (36V)
   */
  digitalWrite(LeftBrakeVoltPin, HIGH);  // Need the higher voltage to activate the solenoid.
  digitalWrite(RightBrakeVoltPin, HIGH); 
  if (state != BR_HI_VOLTS)
  {
    clock_hi_ms = millis();  // keep track of when the higher voltage was applied.
  }
  digitalWrite(LeftBrakeOnPin, HIGH); // Activate solenoid to apply brakes.
  digitalWrite(RightBrakeOnPin, HIGH);
  state = BR_HI_VOLTS;
}
void Brakes::Check()
{
  /* Expected behavior
   *  If 36V has been on too long, relay 3 changes LED on to off, switching from 24 to 12V
   *  If the switch is high, brakes will be released, with both LEDs off.
   */
 
  unsigned long tick = millis();
  if (state == BR_HI_VOLTS && tick - clock_hi_ms > MaxHi_ms)
  {  // Have reached maximum time to keep voltage high
    digitalWrite(LeftBrakeVoltPin, LOW); // Set to lower voltage, which will keep brakes applied
    digitalWrite(RightBrakeVoltPin, LOW);
    state = BR_LO_VOLTS;
  }
}

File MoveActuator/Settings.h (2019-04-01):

#ifndef _SITE_TRICYCLE_SETTINGS_HEADER_
#define _SITE_TRICYCLE_SETTINGS_HEADER_

/*
Settings.h is a site-specific set of trike parameters.
The file SettingsTemplate.h provides examples of how to define parameters,
and shows the necessary parameters.
Only Settings.h should be included from sketches, but not saved in the git repository.
Only SettingsTemplate.h should be saved in the git repository.

After downloading the elcano repository for the first time, copy
libraries/Settings/SettingsTemplate.h
to
libraries/Settings/Settings.h
Add your own trike definitions with a new VEHICLE_NUMBER, and set
VEHICLE_NUMBER to your own new number.
*/

// Dr. Folsom's orange trike.
//#define VEHICLE_NUMBER 1
// Yellow Catrike at the University of Washington at Bothell.
#define VEHICLE_NUMBER 2

#if (VEHICLE_NUMBER == 1)

// Parameters used by Elcano_C2_LowLevel
#define RC_SPEKTRUM 
#undef  RC_HITEC

// Values (0-255) represent digital values that are PWM signals used by analogWrite.

// MIN and MAX ACC set the minimum signal to get the motor going, and maximum allowable acceleration for the motor
#define MIN_ACC_OUT 50
#define MAX_ACC_OUT 235

// MIN and MAX BRAKE_OUT set values to be sent to the brake actuator that controls the brakes on the front wheels
#define MIN_BRAKE_OUT 202
#define MAX_BRAKE_OUT 250

// RIGHT, STRAIGHT, and LEFT TURN_OUT set values to be sent to the steer actuator that changes the direction of the front wheels
#define RIGHT_TURN_OUT 229
#define LEFT_TURN_OUT 127
#define STRAIGHT_TURN_OUT 178

// RIGHT, STRAIGHT, and LEFT TURN_MS are pulse widths in msec received from the RC controller
#define RIGHT_TURN_MS 1000
#define LEFT_TURN_MS 2000
#define STRAIGHT_TURN_MS 1500

// Turn sensors are believed if they are in this range while wheels are straight
// These numbers vary considerably, depending on which sensor angle is set to straight.
#define RIGHT_MIN_COUNT 80
#define RIGHT_MAX_COUNT 284
#define LEFT_MIN_COUNT  80
#define LEFT_MAX_COUNT  284

// Trike specific pins/channels
// Output to motor actuator
#define DAC_CHANNEL 0
// Output to steer actuator
#define STEER_OUT_PIN 7
// Output to brake actuator
#define BRAKE_OUT_PIN 6
// DISK_BRAKE is deprecated, use BRAKE_OUT_PIN

// Trike-specific physical parameters
#define WHEEL_DIAMETER_MM 482
// Wheel Circumference
#define WHEEL_CIRCUM_MM (long) (WHEEL_DIAMETER_MM * PI)
//    Turning radius in cm.
#define TURN_RADIUS_CM 209
//    Turning speed in degrees per ms.
#define TURN_SPEED_DPMS 29700
//    Smallest change in turning angle, in millidegrees
#define TURN_RESOLUTION_MDEG 60
//    Maximum turning angle, in degrees
#define TURN_MAX_DEG 30
//  Motor
#define MOTOR_POLE_PAIRS 23
// maximum allowed speed
#define MAX_SPEED_KPH 15

// Use DAC A
#define THROTTLE_CHANNEL 0

// Parameters used by RC_Control_interrupts
// Indices for information stored in array RC_results
// Channel order differs for different vehicles
#define RC_TURN 1
#define RC_AUTO 2
#define RC_GO   5
#define RC_ESTP 4
#define RC_RDR  5
#define RC_RVS  6
#define RC_BRAKE 3
#define NUMBER_CHANNELS 6

// The assignment of pins used for inputs from the RC controller
// might differ depending on the trike.
#define IRPT_RVS 2
#define IRPT_TURN 21 
#define IRPT_GO 19
//EStop is bound to Channel 5, the red switch on the left side of the controller
//Designed to be toggled on when we want to brake and 
#define IRPT_ESTOP 20
// RDR is used for use this interrupt for the motor
// phase feedback, which gives speed.
#define IRPT_RDR 3
//Switch is actually used for Channel 4(Aka rudder) on the controller
//takes in input from Channel 4 and uses it to control throttle and simple routines
#define IRPT_SWITCH 20

#define IRPT_BRAKE 18

#define IRPT_WHEEL 3

// Currently different interrupts are used for the motor phase feedback.
// These are *temporary*.
#define RC_MOTOR_FEEDBACK RC_RVS
#define IRPT_MOTOR_FEEDBACK IRPT_RVS

#endif

#if (VEHICLE_NUMBER == 2)

// Parameters used by Elcano_C2_LowLevel
#undef RC_SPEKTRUM 
#define  RC_HITEC

// Values (0-255) represent digital values that get converted into PWM signals by analogWrite.

// MIN and MAX ACC set the minimum signal to get the motor going, and maximum allowable acceleration for the motor
#define MIN_ACC_OUT 50
#define MAX_ACC_OUT 227

// MIN and MAX BRAKE_OUT set values to be sent to the brake actuator that controls the brakes on the front wheels
#define MIN_BRAKE_OUT 128
#define MAX_BRAKE_OUT 254

// RIGHT, STRAIGHT, and LEFT TURN_OUT set values to be sent to the steer actuator that changes the direction of the front wheels
#define RIGHT_TURN_OUT 128
#define LEFT_TURN_OUT 254 
#define STRAIGHT_TURN_OUT 192

// Turn sensors are believed if they are in this range while wheels are straight
#define RIGHT_MIN_COUNT 725
#define RIGHT_MAX_COUNT 785
#define LEFT_MIN_COUNT  880
#define LEFT_MAX_COUNT  940
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

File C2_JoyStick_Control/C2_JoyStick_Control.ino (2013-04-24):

/*
  This is a test routine for Elcano.
  It runs on an Arduino Mega 2560 with an Adafruit datalogger shield.
  
  It is based on code by Tom Igoe to use SD card and serial monitor.
  
 The circuit:
 Uses enable switches, joystick, current sensors, and PWM outputs for brakes, steering and motor as
 given in IO_Mega.h

 * SD card attached to SPI bus as follows:
 ** CS - pin 10
 ** MOSI - pin 11
 ** MISO - pin 12
 ** CLK - pin 13
 
 Original SD code created  24 Nov 2010; updated 2 Dec 2010 by Tom Igoe
 
 Adapted 21-29 Feb 2012 by Tyler Folsom
 
 This example code is in the public domain.
 	 
 Status as of 3/13/12:
 Throttle works and is displayed on the 8 LEDs on the front panel.
 All front panel LEDs work except for stopLED.
 Four front panel switches: power and enabling motor, brakes and steering work.
 SD card works, but is sometimes tempermental about displaying on a PC.
 Serial monitor works.
 RTC works with Duemillenove, but RTC hardware does not work on the Mega; use software RTC, which works.
 The throttle controls the servos for steering or brakes.
 Brake servo is physically connected to operate brakes.
 Steering servo has been disconnected from steering linkage. There have been problems 
 with drawing more than 5 amps and blowing the fuse. 
 Traction motor responds to throttle.
 The joystick now works.
 Quiescent current sensors work, though sometimes are zeroed incorrectly.  Increasing current is 
 recognized correctly.
 Traction motor working.
 Joystick is installed and working.
 Quiescent current calculation works on brake and steer; motor current seems high.
 Steering servo works. Steering limits have been set and linkage reattached.
 Wrote routines to ease back on servo requests when too much current is drawn.
 Phsically put everything back together.
 Test all systems on test stand.

 To Do:
 Joystick Center is not read properly. See 2.38V at joystick for center; that voltage does not make it
 to analog input pin 8; continuity problem? Problem bypassed by setting a wide deadband.
 Motor gives jerky response at low speeds; need to smooth it out.
 Brake pusher rod sometimes slips off lever.
 Do a road test.
 Shoot a video and post it.
 */
//#define MEGA
#ifndef TRUE
#define TRUE 1
#define FALSE 0
#endif
//#ifdef MEGA
#include <IO_Mega.h>
//#else
//#include <IO_2009.h> // conflict with chip select
//#endif
#include <SD.h>

// On the Ethernet Shield, CS is pin 4. Note that even if it's not
// used as the CS pin, the hardware CS pin (10 on most Arduino boards,
// 53 on the Mega) must be left as an output or the SD library
// functions will not work.

// Date and time functions using just software, based on millis() & timer

#include <Wire.h>
#include "RTClib.h"

RTC_Millis RTC;

#define FILE_NAME "DataLog.csv"
File dataFile;
struct servo
{
  int QuiescentCurrent; // Background reading of current sensor; counts of analog in: 0 to 1023
  int Current;  // counts of analog in - Quiescent: 0 to 1023
  int mAmp;       // current in milliAmp
  int CurrentSum;  // used to recompute QuiescentCurrent
  int OutputChannel;  // a digital PWM pin number
  int OutputValue;    // counts of PWM out: 0 to 255
  int StartPosition;  // servo is assumed to start here.
  int MaxSlew;   // maximum that OutputValue can change in a second.
  int Stick;    // Joystick reading for motor or throttle; center for brakes
  int EnableSwitch;  // HIGH for cruise or LOW for joystick
};
servo Servos[3];

int QuiescentSamples = 0;
String dataString = String("                                                  ");


const int MOTOR = 0;
const int STEER = 1;
const int BRAKE = 2;
/* Steering servo can handle 44 counts per second;
   Brake servo is good for 88 counts per second.
*/
const int MaxBrakeSlew = 88;  // counts / sec
const int MaxSteerSlew = 44;  // counts / sec
const int LoopPeriod = 100;  // msec
/* The mechanical throttle outputs a voltage between 0.84V (32 counts)
   and 3.55 V (181 counts).
   The motor does not respond until about 1.30 V (66 counts)
*/
const int MaxMotorChange = (70*LoopPeriod)/1000;  // counts per step for motor
const int MaxBrakeChange = (MaxBrakeSlew*LoopPeriod)/1000; // counts per step
const int MaxSteerChange = (MaxSteerSlew*LoopPeriod)/1000;
const int MotorFull = 186;   // fully on for PWM signals
const int MotorMin  = 66;
const int MotorOff = 0;
const int FullThrottle =  179;   // 3.5 V
const int MinimumThrottle = 39;  // Throttle has no effect until 0.75 V
const int BrakeOn = 127;  
const int BrakeOff = 255;
const int HardLeft = 255;
const int HalfLeft = 223;
const int Straight = 191;
const int HalfRight = 159;
const int HardRight = 128;
/*  Servo range is 50 mm for brake, 100 mm for steering.
    Servo is fully retracted on a pulse width of 2 ms;
    fully extended at 1 ms and centered at 1.5 ms.
    There is a deadband of 8 us.
    At 12v, servo operating speed is 56mm/s with no load or
    35 mm/s at maximum load.
    
    The Arduino PWM signal is at 490 Hz or 2.04 ms.
    0 is always off; 255 always on. One step is 7.92 us.
    
*/

/*---------------------------------------------------------------------------------------*/ 
// Bring the vehicle to a stop.
// Stop may be called from an interrupt or from the loop.
void Halt()
{
   analogWrite(TractionMotor, MotorOff);
   analogWrite(DiskBrake, BrakeOn);
   Servos[MOTOR].OutputValue = MotorOff;
   Servos[BRAKE].OutputValue = BrakeOn;
   digitalWrite(StopLED, HIGH);
}
/*---------------------------------------------------------------------------------------*/
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

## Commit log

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2011-03-15 Temporarily swap Motor and Steer pins. Modify tests.
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2011-03-20 Introduced Elcano_simulator and modified routines to provide entry points; Replaced Serial.c with Serial.cpp.
    [Elcano_C3_Pilot.pde, Elcano_C4_Planner.pde]
2011-05-22 Moved files to Documentation directory; Updated C2 Controls with tests.
    [Power.xls, Wiring.xls, Wiring_C2.xls]
2011-05-22 Removed files that have been transfered to sub-directory.
    [Power.xls, Wiring.xls]
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2012-02-27 Swapped pins 22 and 26 to enable motor and steering; now matches hardware.
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2012-02-28 Swapped D22 and D26; Added sheet for power.
    [Wiring_C2Mega.xls]
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2012-04-19 C5 gives wiring for obstacle detection on a stand-alone Arduino. C6 incorporates obstacle detection into the Navigation processor.
    [Wiring_C5.xls, Wiring_C6Mega.xls]
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2012-04-19 Documentation for navigation system. Updated Bill of Materials; source for Elcano_BOM.html version.
    [Elcano_BOM.xls]
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2012-05-15 Major rewrite to replace C3 pseudocode with real code.
    [Elcano_C3_Pilot.ino, Elcano_C4_Planner.ino]
2012-05-18 Added WhereAmI and distance routines; replaced bearing with unit vectors.
    [Elcano_C3_Pilot.ino]
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2012-05-31 Updated Navigator to use Common.h .cpp, which replace GPS.h, .cpp.
    [Elcano_C6_Navigator.ino]
2012-06-30 Introduced feedback from steering and brake, replacing speed and speed limit.
    [Wiring_C2Mega.xls]
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2012-08-23 Corrected feedback pin names.
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2013-02-28 Schematic for PCB wiring Arduino headers to DB25/15 sockets.
    [Arduino_backplane.brd]
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2013-03-07 Include DAC and new headers to steering and brake headers.
    [Arduino_backplane.brd]
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2013-03-07 Added Eagle schematic and board layout for Megashield DB. Schematic is near final, but board needs a lot of work.
    [Arduino_backplane.brd, Arduino_backplane.sch]
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2013-03-08 Moved components for better routing; corrected connection errors.
    [Arduino_backplane.brd, Arduino_backplane.sch]
2013-03-09 Corrected some overlaps
    [Arduino_backplane.brd, Arduino_backplane.sch]
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2013-03-11 Arduino pins placed correctly; 100% routed. SOme errors.
    [Arduino_backplane.brd]
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2013-03-20 Included holes for mounting Mega, board cutouts, renamed connectors. Signals to front panel have been swapped. Connector names have changed.
    [MegaShieldDB.brd, MegaShieldDB.sch]
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2013-03-22 Mirrored Arduino pins for bottom mount. Added Wheel Revolution with pull-up resistor.
    [MegaShieldDB.brd, MegaShieldDB.sch]
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2013-04-12 New documentation of PCB board; added notes on signals;PCB board layout as built.
    [Arduino_backplane.brd, MegaShieldDB.brd, MegaShieldDB.sch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]
2013-04-23 Cost based on lead-acid. Catrike Dash is no longer available; needs to be updated.
    [Elcano_BOM.xls]
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2013-05-07 Corrected Base/Emitteron Q1, Q2
    [MegaShieldDB.brd, MegaShieldDB.sch]
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2013-05-16 Servo calibration. Rewritten & untested -- pushing so it can be looked at. (Previous commit had this message on the wrong file.)
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2015-03-08 fixed the file format descriptions
    [Elcano_C4_Planner.ino]
2015-03-12 Fixed memory overwriting due to use of String class. Replaced with char*s.
    [Elcano_C4_Planner.ino]
2015-03-13 Added post-update benchmark and fixed original benchmark test.
    [Elcano_C4_Planner_Benchmark_2.ino]
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2015-03-30 Code and documentation from CSS 427 winter 2015 Trio V2 board team project. Team members are Kelley Welsh and James Finley, and they are the actual authors of this commit. Co-Authored-By: Kelley Wels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
    [MegaShieldTrioV2.brd, MegaShieldTrioV2.sch]
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2015-07-09 Performance Enhancements
    — Additional bit manipulation functions added (Line 93)
    — Code structure fixed to easily enable/change functionality of program
    — Reduce repetitiveness code
    — Removed superfluous macros
    [Elcano_C5_Sonar.ino]
2015-07-18 Additional Features Added
    - Modified range int array into a matrix array
    - Data Table can be sorted in order using the method sortArray (Bubble
    Sort)
    - Update - Replaced sortArray method with Quick Sort Algorithm
    - Created a method that will find the Mode in a sorted array
    - writeOutput now displays all samples and the mode/medium
    - Using F() to store any char array into flash memory
    Warning - Updates with the findMode and writeOutput methods have not
    been tested
    [Elcano_C5_Sonar.ino]
2015-07-19 Fixed findMode Bug
    — Find Mode method has been fully tested allowing for the correct MODE
    or MEDUIM to be found
    — Equal and less than zero values will not be counted in the final
    results if a MODE/MEDUIM is found,
    — If a zero is returned, there is no data that is qualified in the array
    [Elcano_C5_Sonar.ino]
2015-08-13 Fixing RC_Control_Interrupts, this check in is verified to work against the yellow bike
    [RC_Control_interrupts.ino]
2015-08-17 New lines for reverse, regen braking on X3. Document alternate wiring on X5 for vehicle #2.
    [Wiring_C2PCB.xls]
2015-08-17 Push to GitHub
    Needs to be commanded and fix an error with one of the arrays
    [Elcano_C5_Sonar.ino, algorithms.ino, communication.ino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]
2015-08-31 Computation of conditional probability of an orange cone pixel given its color. Split orange cone and background images for training set (half of the original images). Cone and background image histo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
    [backgrounds.csv, cones.csv, ocp.csv]
2015-09-04 Split out scripts for computing the conditional probability and converting an image. Update histograms and probability with a few more training images.
    [backgrounds.csv, cones.csv, ocp.csv]
2015-09-11 Update Elcano C5 & C6 Batch
    - Added Template Sonar SPI Master file
    - Tiny Bug with Elcano_C5_Sonar interruption for PW_OR1 Fixed
    - Refactor Elcano_C6_Compass files
    [Elcano_C5_SPI_Master.ino, Elcano_C5_Sonar.ino, algorithms.ino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]
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2015-09-24 Switch to representing probabilities as 8-bit grayscale values in the range 0-255. This is more compact than 32-bit floats and provides sufficient granularity.
    [ocp.csv]
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2015-10-08 Revert Elcano_C6_Navigator.ino
    File was merged over with an older version, and reverting back to what
    Jordan had written adding the compass component to the navigator.
    [Elcano_C6_Navigator.ino]
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2015-10-10 Assorted fixes, e.g. give rising & falling edge interrupts their own variables, operator precedence,...
    [Elcano_C2_LowLevel.ino]
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2015-12-09 Corrected index for PID
    [Elcano_C2_LowLevel.ino]
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2016-03-04 Documentation for RC; in loop, changed check on DONE from if to while; improved printed info; verified #2 motion control on right joystick; E-Stop is off with left joystick down.
    [Spektrum dx6i.xls]
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2016-03-04 Fixed Speedometer: right diameter for #2, right pin number for RC shield, faster minimum speed goes to zero faster.
    [Elcano_C2_LowLevel.ino]
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2016-04-30 Implemented Pat's method of using hub phase to find the speed. Documentation file is for using screw connectors.
    [KellyConnections.xls]
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2016-06-16 Created/added test file for 4 digit (speedometer) display
    Got the 4 digit display working. The trick was that the Cursor for entering the digits is saved on the atmel processor embedded on the device, so it is a saved state, even if you reset the main arduino. To get around this, I set the cursor to the left-most digit on setup.
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2016-07-03 Corrected 7seg display serial line #
    [Elcano_C2_LowLevel.ino]
2016-07-06 Basic Obstacle Avoidance
    Adds basic obstacle avoidance logic to the C3_Pilot module. Currently
    can't communicate with the C5_Sonar module, but only needs to take in
    the array of ranges from that board.
    [ObstacleAvoidance.ino]
2016-07-17 fixed issues with pull request
    [Elcano_C4_Planner.ino]
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2016-07-31 Move more settings to Settings. Fix two bugs in LowLevel.
    [Elcano_C2_LowLevel.ino, MoveActuator.ino, RC_Control_interrupts.ino]
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2016-08-09 Fixed variable bugs in calibrateRC
    [Elcano_C2_LowLevel.ino]
2016-08-10 bug fixes after code review
    [Elcano_C3_Pilot.ino, ObstacleAvoidance.ino]
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2016-08-13 Incomplete bug fixes to compare
    [Elcano_C2_LowLevel.ino]
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2016-08-17 I don't know what changed here, but it doesn't look broken.
    [MoveSteeringSerial.ino]
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2016-08-24 Revert "fuzzy"
    This reverts commit 21be4841e2b539880edeb9dd5359eef493e5daee.
    [Elcano_C6_Navigator.ino]
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2016-09-07 Fixed convertDeg function to not use magic numbers, and added relevant values to SettingsTemplate.
    [Elcano_C2_LowLevel.ino]
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2016-09-09 Fix 2 Low Level
    [Elcano_C2_LowLevel.ino]
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2016-09-10 Fixed various bugs in squareRoutine. Still prototype!
    [Elcano_C2_LowLevel.ino]
2016-09-12 Replaced micros() calls with millis() in loop function; delay() takes values in milliseconds, so we were delaying a thousand times as long as we needed to.
    [Elcano_C2_LowLevel.ino]
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2016-09-14 Potentially weeded out nextTime corruption (no promises!). Added sanity checks for multiple points of failure. Current status also includes several unmemorable changes and modification by other parti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
    [Elcano_C2_LowLevel.ino]
2016-09-16 Fix immediate API breakage
    Currently, many of the subsystems need to be rewritten to use the new
    API. This commit should fix COMPILATION errors, so that everything still
    works for the demo. However, larger changes will be needed going
    forward.
    [Elcano_C2_LowLevel.ino, Elcano_C3_Pilot.ino, Elcano_C4_Planner.ino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]
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2016-10-07 Fix buffer overruns and loop timing. Add clock overflow handling. Remove spinloop and move test for receipt of RC data to where it's used. Remove extraneous comments and add many ToDos.
    [Elcano_C2_LowLevel.ino]
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2016-10-14 Update comments. Explain how we want the live throttle versus doing a test routine versus stopping to work. No code change, as we've decided the current behavior is correct.
    [Elcano_C2_LowLevel.ino]
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2016-11-10 Fixed merge of LowLevel, cleaned up PIDTest
    [Elcano_C2_LowLevel.ino]
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2017-01-03 rcTest and added mapThrottle to LowLevel
    Added rcTest program, updated C2_LowLevel with mapThrottle to speed
    function
    [Spektrum dx6i.xls]
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2017-01-18 Fix ebrake in figure8Routine
    [Elcano_C2_LowLevel.ino]
2017-01-18 Fixed integer division error
    [Elcano_C2_LowLevel.ino]
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2017-01-25 Bugfixes and debugmode to time based brake library
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2017-02-02 Revert "RC changes"
    This reverts commit 2287bc5949dd4a6cce2bc741de03bd1be1657c5e.
    [Elcano_C2_LowLevel.ino]
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2017-02-23 new libraries, replace your old one completely
    [Elcano_C6_Navigator.ino]
2017-02-27 Elcano C2 using correct ThrottlePid
    [Elcano_C2_LowLevel.ino, Elcano_C3_Pilot.ino]
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2017-03-09 Move Fixed Distance and Square Routine completed
    [Elcano_C2_LowLevel.ino, Elcano_C3_Pilot.ino]
2017-03-14 Move fixed distance ready
    [Elcano_C2_LowLevel.ino, Elcano_C3_Pilot.ino, Elcano_C6_Navigator.ino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]
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2017-05-23 Updated the mission to the correct mission
    [Elcano_C4_Planner.ino]
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2017-07-19 Fixed bugs, added pixel location, distance, degree
    The condition that checked for hulls between 3 and 10 had incorrect
    syntax. Fixed some of the magic numbers for color/shape thresholding.
    Added pixel location of cones by the center of their bounding rectangle.
    Added distance and degree based on Joe's calculations.
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2017-12-14 Minor changes to Sweep Obstacle Detector
    - Added preprocessor switch for debug mode
    - Fixed checks for motor speed and sample rate
    - Formatting changes
    [Sweep_Obstacle_Detector.ino]
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2018-06-14 New PCB for HighLevel and LowLevel; Low level is not quite as built; needs to be updated
    [High-Level PCB v3.0.brd, High-Level PCB v3.0.sch, LowLevelv2.brd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]
2018-11-16 The loop timing code is buggy. It uses an unsigned variable for a signed quantity that is almost certainly negative. Observed symptom was that the loop went through one pass then hung. That is consis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
    [Elcano_C2_LowLevel.ino]
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2018-12-23 Adding SCH and BRD files for RC Transmitter unit. This board is designed for an arduino micro, two joysticks, indicator LEDs, (power, estop, and auto) switches, and a 3-pin ASK radio.
    [rc-tx-board-V1.brd, rc-tx-board-V1.sch]
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2019-04-01 Removed/ Added to correct folder
    [Elcano_C2_LowLevel.ino]
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2019-04-01 Initial commit of LLv3 snapshot
    Also includes updated (and contained) elcanoParts library
    [LowLevelv3.brd, LowLevelv3.sch]
2019-04-01 electronics update!
    moved a lot of stuff to get the board smaller, added ground planes, added CANbus 3-pin header, fixed all the silkscreening
    [LowLevelv3.brd, LowLevelv3.sch]
2019-04-01 added PWM output on steering header and 120ohm terminating resistor for CAN
    forgot to commit this...
    [LowLevelv3.brd, LowLevelv3.sch]
2019-04-01 removed accidental debugging Mega, added a handful of vias to fix GND orphans
    [LowLevelv3.brd, LowLevelv3.sch]
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2019-04-01 minor changes to vehicle and lowlevel
    next step fix interpolation
    [Brakes.cpp, Elcano_C2_LowLevel.ino]
2019-04-01 fixed silkscreen in old v2
    [LowLevelv2.brd]
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2019-04-01 fixed spelling error in folder name
    [Brakes.cpp]
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2019-04-01 Many LLBv3 updates in one!
    re-arranged inerrupt pins to share a PCI ISR, added RC circuit to MCP2515 per datasheet, replaced impossible capacitor, re-arranged oscilator layout
    [LowLevelv3.brd, LowLevelv3.sch]
2019-04-01 LLBv3 updates
    replaced all thru-hole res/cap with SMD parts, arranged part grids, re-routed the board
    [LowLevelv3.brd, LowLevelv3.sch]
2019-04-01 fixed bad late night code
    [Brakes.cpp, Settings.h, SteeringController.cpp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]
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2019-04-01 LLBv3 routing overhaul
    applied restriction polygons and added many vias to prevent GND airwires
    [LowLevelv3.brd, LowLevelv3.sch]
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2019-04-01 re-routed watchdog from digi-5 to DB15 thru middle instead of along edge
    [LowLevelv3.brd]
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2019-04-01 Updates to board, schematic, library
    added 4.7k pullup to odometer and took first steps towards replacing the arduino headers with custom component with correct pin names.
    [LowLevelv3.brd, LowLevelv3.sch]
2019-04-01 corrected PCINT pin mapping
    moved pretty much every interrupt pin to A8-A15, which had the secondary benefit of greatly reducing their trace length.
    [LowLevelv3.brd, LowLevelv3.sch, Pin Mapping.xlsx]
2019-04-01 board cleanup, via removal, silkscreen tidying
    * Changing size of almost every 'tvalue' item
    * slightly tweaked trace location to allow for greater ground plane coverage
    * removed redundant ground vias
    * began renaming devices for clarity
    [LowLevelv3.brd, LowLevelv3.sch]
2019-04-01 lots of renaming and slight position changes
    * renamed caps and resistors to make populating the board a little easier
    * moved silk around to try and be a little more coherent
    * slight copper adjustments to get more ground fill
    [LowLevelv3.brd, LowLevelv3.sch]
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2019-04-01 Made recommended changes
    Notes on Low Level Code
    Good organization with Vehicle, Brake, ThrottleController etc. classes.
    The only thing in the main loop is vehicle.update, which checks the brakes, computes the speed and the steering angle. It does not set the throttle, so there is no way to make the trike go. It does not set the steering angle or apply the brakes. How is the vehicle controlled? Where is communication with the Remote Control or High Level?
    I added the existing communication code from the elcano/elcano repo but this is the section we will be reworking for can
    There are two reasons to avoid doubles. I would prefer to see doubles eliminated from the code, exce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
    [Brakes.cpp, Elcano_C2_LowLevel.ino, Settings.h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]
2019-04-01 Checkpoint for first PCB order
    * few minor routing changes
    * extended a 1x8 to a 1x10 because some Mega boards have two more pins on one header.
    * added partial bill of materials
    [BoM.xlsx, LowLevelv3.brd, LowLevelv3.sch]
2019-04-01 swapped 0.2uF for 0.1uF, updated BoM
    [BoM.xlsx, LowLevelv3.brd, LowLevelv3.sch]
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2019-04-01 first foray into sorting the electronics folder and filtering out obselete designs
    Do note that files in folders may not have access to the ElcanoParts library
    [BoM.xlsx, High-Level PCB v3.0.brd, High-Level PCB v3.0.sch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]
2019-04-01 expanded copper for relay module, moved drills for odometer away from board edge
    [LowLevelv3.brd]
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2019-04-01 LLBv3 corrections
    Fixed silk-via overlapping regions.
    Fixed reset button schematic/wiring, now connects reset to ground.
    Swapped CAN differential pair pinout by fixing the part in the library and re-routing the board.
    Moved some surface mount parts to better propagate the ground plane.
    Added on-silkscreen documentation for CAN and relay pinouts.
    Added power-OK led and its resistor.
    Changed board outline, reduced area and added two corner cuts.
    [LowLevelv3.brd, LowLevelv3.sch]
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2019-04-01 LLBv3.1 changes
    Rerouted high-current relay circuit to handle swapped NC/NO pins.
    Replaced 10-pin connector with 8-pin RJ45 modular jack. Expensive mistake.
    Added debug LED on pin D13.
    Added test points for steering header.
    Silkscreen and routing corrections.
    [LowLevelv3.brd, LowLevelv3.sch]
2019-04-01 Corrections to silkscreen, added testpoints
    Fixed silkscreen errors around the relay terminals, added symbols.
    Added testpoints and easily cut traces for steering header ground pins, for future expandability options.
    [LowLevelv3.brd, LowLevelv3.sch]
2019-04-01 Removed DACB from the DB15 connector. Pin 13 will now be used by the manual throttle as a 5V source.
    Also added a pair of test points for DAC channels A & B.
    [LowLevelv3.brd, LowLevelv3.sch]
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2019-04-01 Restored DACB to the DB15, but now on pin 15. Removed watchdog from DB15.
    Minor changes to silkscreen and trace routing.
    [LowLevelv3.brd, LowLevelv3.sch]
2019-04-01 Added document to describe the steering header pin mapping on a CAT5E
    [Steering pinout on cat5.csv]
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2019-04-01 Minorsilkscreen updates
    Named testpoints
    Swapped 10k for 0 ohm resistor on reset button
    [LowLevelv3.brd, LowLevelv3.sch]
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2019-04-01 fixed classes for can interrupts, made instances static
    [Brakes.cpp, Elcano_C2_LowLevel.ino, Settings.h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]
2019-04-01 bug fix
    wrong argument in map
    [SteeringController.cpp]
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2019-04-01 Corrected pin mapping document for steering PWM pin
    [Pin Mapping.xlsx]
2019-04-01 fixed steering
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

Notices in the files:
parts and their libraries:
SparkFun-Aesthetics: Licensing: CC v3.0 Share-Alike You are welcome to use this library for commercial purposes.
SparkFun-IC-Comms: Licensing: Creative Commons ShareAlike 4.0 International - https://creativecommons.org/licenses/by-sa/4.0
